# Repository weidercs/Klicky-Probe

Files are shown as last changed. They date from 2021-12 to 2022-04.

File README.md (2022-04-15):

# Klicky Probe
Microswitch probe with magnetic attachment, primarily aimed at CoreXY 3d printers.

Initially it was focused on the [Voron printers](https://vorondesign.com/) (V2.4, V1.8, Trident, V0) and derivatives, now it's been restructured to better allow other printers to be documented here.

**ATTENTION**
If you come from Voronusers please read the updated Klipper configuration on this repository

The objectives for this project are:
- drop in replacement for Omron TL-Q5MC2 or PL-08N2 (you don't need to replace the toolhead), replacement of BLtouch probes
- soldering not required
- minimal adjustments required
- be able to detect all the print surfaces
- be as close to the hotend tip as possible
- highly repeatable and accurate probes
- less temperature variations
- no melting of its parts
- cheap to build
- reuse spare parts if possible

Most of the Klicky probe users are using klipper, there are some macros in here that ease the probing process, by automating the attach, dock and use of the probe.

Some work has been developed to have the same functionality on RRF.

It can also be used with the [automatic Z calibration](https://github.com/protoloft/klipper_z_calibration) klipper plugin to effectively calculate the Z offset from the probe and from the Z endstop if your printers supports a Z endstop triggered by the nozzle (like most Voron's do)

The inspiration for the Klicky Probe comes from the [Quickdraw](https://github.com/Annex-Engineering/Quickdraw_Probe) and the [Euclid probe](https://github.com/nionio6915/Euclid_Probe), it uses some concepts from each of the projects.

Updated instructions provided by StefanRaatz.
oc_geek and TurBoxxs were also a great help in refining and testing the CAD files.
Garrettwp provided the initial revised macro files.
User richardjm revised the macro variables and added some functions.
Mental created the initial macro and one of the first magnetically attached microswitch probes.

Without them, and some others this effort would not be in the current state, many thanks to them all.

It is working very well, if you decide to use it, give me feedback, either here, or on discord, my discord user is JosAr#0517.

If you want to donate something regarding this project, use this [link](https://paypal.me/Josar154) or [__Buy me some ABS!__](https://www.buymeacoffee.com/JosAr), thanks

# Upgrading from an earlier version

If you are upgrading from an earlier version, check the [klipper macros](./Klipper_macros) folder, it contains update instructions.

# Printers With detailed instructions and specific parts (by support order)

The specific parts with install, configuration, troubleshoot and recommended settings can be found on each printer page, linked below.

[Voron v2.4](./Printers/Voron/v1.8_v2.4_Legacy_Trident)

[Voron v1.8](./Printers/Voron/v1.8_v2.4_Legacy_Trident)

[Voron Legacy](./Printers/Voron/v1.8_v2.4_Legacy_Trident)

[Voron Trident](./Printers/Voron/v1.8_v2.4_Legacy_Trident)

[Voron v0](./Printers/Voron/v0)

[VCore-3](./Printers/Ratrig/VCore3)

[MercuryOne](./Printers/ZeroG/Mercury_One)

There are also [docks and mounts submitted by users](./Usermods) to support other printers and toolheads, you should check it out.

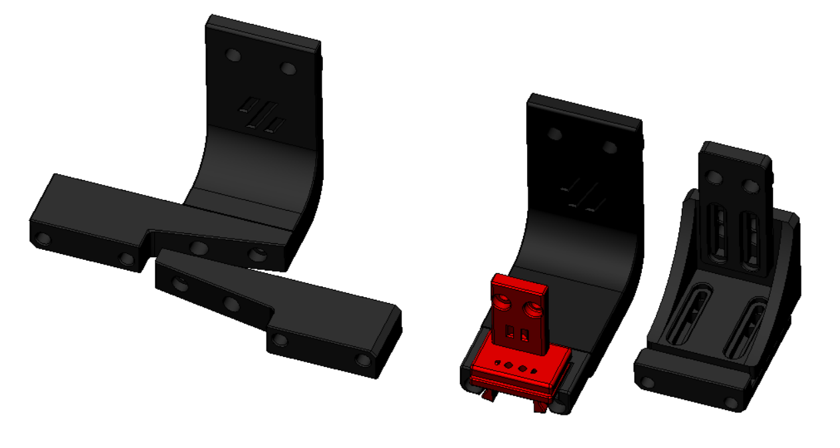
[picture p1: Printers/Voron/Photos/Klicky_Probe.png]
Klicky Probe image
klicky early version.

# Klicky components

All the compatible printers require:

* Toolhead mount (the thing that the probe attached to when it's being used)
* Klicky probe (there are three versions, all are interchangeable and compatible, more information on the specific printer page), what actually is used to probe the bed
* Probe dock (all the printers use the same)
* Probe dock mount (what attaches to the printer to dock the probe when not in use)

The CAD with all the files is located [Here](./CAD)

Common Klicky STL's (parts that are common to all the printers)  are located [here](./Base_STL).
Printer specific STL are in each printer directory.

The klipper macros are [here](./Klipper_macros), the RRF [here](./RRF_macros).

## Probe accuracy

The probe accuracy output is better than a range of 0.025mm (difference between highest and lowest), and a standard deviation of 0.01mm.

## Print Settings

There are no need for supports, recommended settings are 4 perimeters/top/bottom, at least 23% infill, the STL's are already oriented, you only need to send them to the slicer.

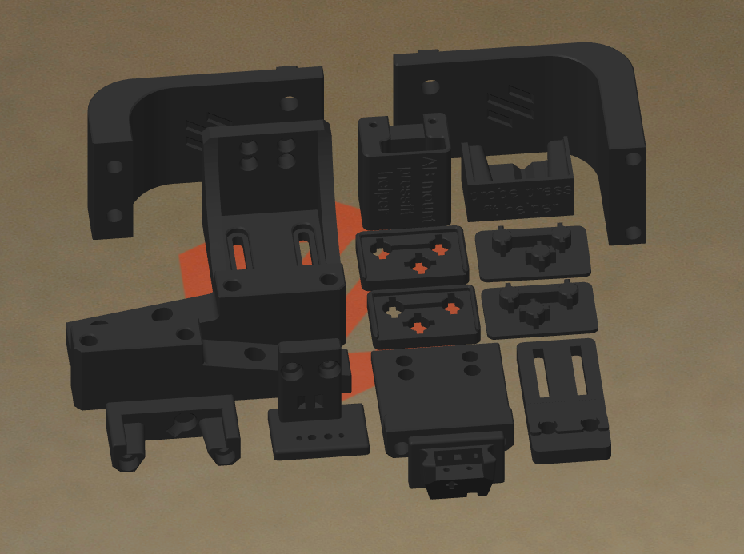
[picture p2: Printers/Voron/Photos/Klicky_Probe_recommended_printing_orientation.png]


Each printer family/version has it's own mounting options, Bill of Materials, assembly instructions and dock/attach setup.

# General Bill of Materials (BOM)

Tools:

- 1.5mm Drill (optional)
- Multimeter to check for Continuity 
- Super Glue
- Soldering Iron for the heat inserts

Probe BOM:

- 1x microswitch (the omron D2F-5 or D2F-5L (removing the lever) is recommended), D2F-1 and similar sizes microswitch also work
- 2x M2x10 mm self tapping
- some 6 mm x 3 mm magnets (it ranges from 8 to 10)
- some m5 screws
- some m3 screws
- some m3 heat inserts
- some m3 nuts

# Sourcing guide

To get the best experience, please consider purchasing from the trusted list of suppliers bellow.

[trusted suppliers list](./Sourcing.md)

# Assembled Klicky Probe on a Voron v2.4

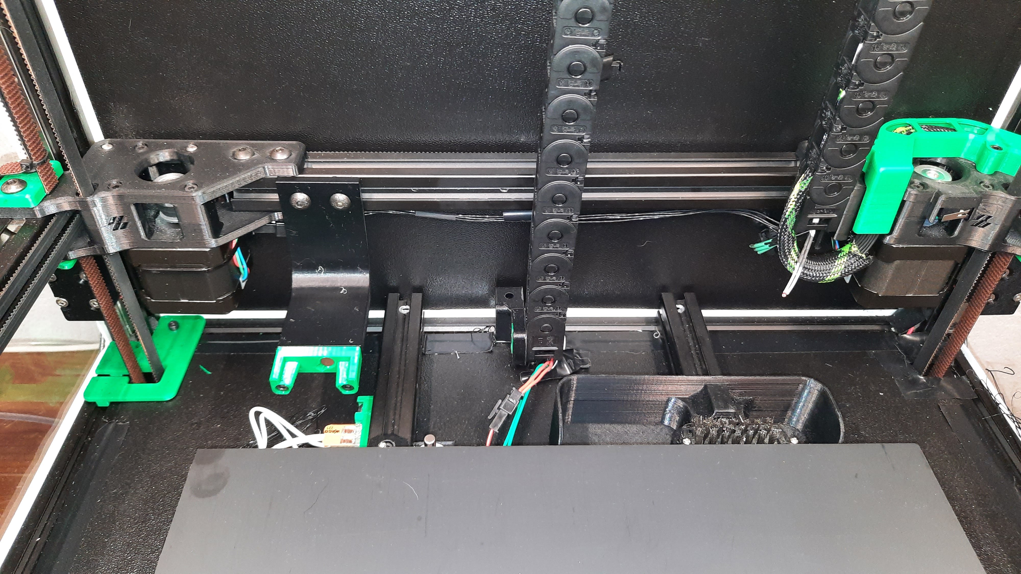
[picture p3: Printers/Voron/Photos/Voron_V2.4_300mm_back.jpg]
Assembled Klicky Probe
# 

# Dock and undock video

https://user-images.githubusercontent.com/16675722/122302371-eb9c4e00-cef9-11eb-91d3-3aded131bae0.mp4

It is working very well, if you decide to use it, give me feedback, either here, or on Voron discord, my discord user is JosAr#0517.

By standing on the shoulders of giants, lets see if we can see further.

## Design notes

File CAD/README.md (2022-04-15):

CAD files

KlickyProbe_v2_v44
Initial release of the V2 klicky, with a 2mm shorter probe dock. Probe dock mounts adjusted accordingly

KlickyProbe_v2_v50
corrected dock mount fixed distance, it was 2 mm short

KlickyProbe_v2_v51
added MercuryOne probe dock

KlickyProbe_v2_v53
added VCore3 probe dock and EVA mount

KlickyProbe_v2_v54
added V0.1 Mosquito Cowling

KlickyProbe_v2_v55
corrected V0.1 integrated Mosquito Cowlings

KlickyProbe_v2_v56
updated the probe dock to have back inserted magnets, it's not possible now for the dock magnet to touch the probe one

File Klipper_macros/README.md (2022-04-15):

# Klipper macros

These macros are  based on the great Annex magprobe dockable probe macros "#Originally developed by Mental, modified for better use on K-series printers by RyanG and Trails", kudos to them.
That macro as since evolved into a klipper plugin that currently is pending inclusion in klipper, more information [here](https://github.com/Annex-Engineering/Quickdraw_Probe/tree/main/Klipper_Macros)

Would alse like to thank the Voron discord community and VoronDesign for all the work, suggestions and support that they have given to improve on the macros.

## Updating from an earlier version

While you should read these instructions to the end, as the necessary helper functions are now split on different files and it's better explained below, as a current user of the klicky macros, it's easier to configure.

The first macro on the old klicky-probe.cfg contained all the necessary variables, you should the values you changed one by one to the new klicky-variables.cfg, the most important are these ones:

```python
# if you do not have any of these variables, read the explanation on klicky-variables.cfg and the setup of the macros on your respective printer, this is a quick start quide
variable_enable_z_hop           # set this to false for beds that fall significantly under gravity (almost to Z max)
variable_max_bed_y              # bed max y size
variable_max_bed_x              # bed max x size

variable_z_endstop_x            # copy this value over your old file
variable_z_endstop_y            # copy this value over your old file

variable_docklocation_[x,y,z]   # copy this value over your old file
Variable_dockmove_[x,y,z]       # use 40,0,0 it's the old default
Variable_attachmove_[x,y,z]     # use 0,30,0 it's the old default
```

Now if you use auto-z calibration, you also should copy z-calibration.cfg to klicky-z-calibration.cfg and remove the z-calibration.cfg include in printer.cfg.

## New installation

The macros are currently separated by function, there is klicky-probe.cfg that should include the remaining files, this both keeps klipper's printer.cfg cleaner and allow for backward compatibility.

The remaining files are the klicky-macros.cfg that stores all the general macros (like the dock and attach macros, this file is required on all the printers), the klicky-variables.cfg where it's necessary to configure the dock location and do other printer specific configurations and the klipper helper files for specific functions.

The helper files work by expanding the standard klipper function with a attach and dock command, so that you can use all the klipper commands without the need to manually attach and dock the printer.

Right now the macros are divided in multiple files, that way it is much easier to upgrade, configure and maintain

| File | v2.4 | v1.8 | Legacy | Trident | v0 | Tiny-M | V-core3 | MercuryOne |
| --- | :---: | :---: | :---: | :---: | :---: | :---: | :---: | --- |
| klicky-probe.cfg | :heavy_check_mark: | :heavy_check_mark: | :heavy_check_mark: | :heavy_check_mark: | :heavy_check_mark: | :heavy_check_mark: | :heavy_check_mark: | :heavy_check_mark: |
| klick-variables.cfg | :heavy_check_mark: | :heavy_check_mark: | :heavy_check_mark: | :heavy_check_mark: | :heavy_check_mark: | :heavy_check_mark: | :heavy_check_mark: | :heavy_check_mark: |
| klicky-bed-mesh-calibrate.cfg | :heavy_check_mark: | :heavy_check_mark: | :heavy_check_mark: | :heavy_check_mark: | :heavy_check_mark: | :heavy_check_mark: | :heavy_check_mark: | :heavy_check_mark: |
| Klicky-quad-gantry-level.cfg | :heavy_check_mark: | :x: | :x: | :x: | :x: | :x: | :x: | :x: |
| Klicky-screws-tilt-calculate.cfg | :x: | :heavy_check_mark: | :heavy_check_mark: | :x: | :heavy_check_mark: | :heavy_check_mark: | :x: | :grey_question: |
| klicky-z-tilt-adjust.cfg | :x: | :heavy_check_mark: | :heavy_check_mark: | :heavy_check_mark: | :x: | :x: | :heavy_check_mark: | :heavy_check_mark: |

* klicky-probe.cfg (includes all the necessary files in klipper)
* klick-variables.cfg, stores all the Klicky variables, printer specific, should not be necessary to update very often
* klicky-bed-mesh-calibrate.cfg, bed mesh helper scripts, assumes bed mesh is already configured, includes a commented example, further help on setup [here](https://www.klipper3d.org/Bed_Mesh.html#bed-mesh)
* Klicky-quad-gantry-level.cfg, Quad Gantry Level helper script, allows on machines with four Z independent motors to level the bed automatically, assumes QGL is already configured (it's used on a V2.4 to level the gantry relative to the bed), further help [here](https://www.klipper3d.org/Config_Reference.html?h=quad#quad_gantry_level)
* Klicky-screws-tilt-calculate.cfg, screws tilt adjust helper script, knowing where the bed screws are, it will assist in leveling the bed by calculating on the number of times each screw should be rotated, assumes that the configuration is already defined, further help on setup [here](https://www.klipper3d.org/Manual_Level.html#adjusting-bed-leveling-screws-using-the-bed-probe)
* klicky-z-tilt-adjust.cfg, Z tilt adjust helper script, allows on machines with two or three Z independent motors to level the bed automatically, assumes that the configuration is already defined, further help on setup [here](https://www.klipper3d.org/Config_Reference.html?h=z_tilt#z_tilt)
* klicky-specific.cfg, place to put other configurations specific to your printer, like probe or bed mesh klipper configuration

Some printers, like the Voron v0 or Tiny-M don't have the probe as a standard configuration, so in those printers documentation there are extra klipper configurations that you need to use in order to configure the actual probe.

## printer.cfg configuration 

Download the appropriate files (or the zip containing them all and delete the ones that are not relevant) and upload it to your klipper Config folder.

```
cd ~/klipper_config/
wget https://raw.githubusercontent.com/jlas1/Klicky-Probe/main/Klipper_macros/Klipper_macros.zip
unzip Klipper_macros.zip
```

Check the klicky-probe.cfg, remove or comment the macros that are not required for your printer or that you do not want to implement.
Edit klicky-variables.cfg (there are printers specific recommendations on the printer configuration page) for klicky to operate properly.

There are some configurations that need to be checked, otherwise your will run into **out of range** problems, that is by design.

Open your printer.cfg file, comment out *safe_z_home* or *homing_override*, if you have them (the macros will take care of homing) and add the following line before the "Macros" Section.

`[include klicky-probe.cfg]`

It should look like this:

```
#####################################################################
# 	Macros
#####################################################################
[include klicky-probe.cfg]
```

You now need to configure the probe pin, that is printer specific, and the details are on your printer configuration guide.

Regarding you print start and end macros, with the helper scripts implemented, they do not need to be changed.

If however you would like to reduce the times that the toolhead attaches and docks the probe, you can use Attach_Probe_Lock that prevents the probe to be docked after an operation that normally would dock the probe.

**BEWARE that the probe may hit the bed depending on what you are doing**.

When you don't need the probe attached anymore, run Dock_Probe_Unlock to dock and unlock the probe.

## Pre and Post macros for dock operations

If your setup requires a custom move, a macro to be called before attaching and docking, there are two macros \_DeployDock and \_RetractDock that are executed (if they are configured) when it's required for the dock to be ready for docking and attachment operations.

## XY Sensorless homing 

If you are using sensorless homing, and have your own X and/or Y homing macros, you can use override the klicky macros behavior with your very own _HOME_X and _HOME_Y macros.

If they exist on your klipper configuration, klicky macro will use them instead of the default G28 commands.

## Advanced users

**Beware going forward, you will leave the safety that the macros provide**

I recognize that some users are very technical and may want to write custom macros, so here are the only commands that you need to  attach and dock the probe, without any fail safes or checks.

### Probe attach commands

```python
# Probe entry location
G0 X{docklocation_x|int - attachmove_x|int - attachmove2_x|int} Y{docklocation_y|int - attachmove_y|int - attachmove2_y} F{travel_feedrate}
# Attach probe
G0 X{docklocation_x|int - attachmove2_x|int} Y{docklocation_y|int - attachmove2_y} F{travel_feedrate}
G0 X{docklocation_x} Y{docklocation_y} F{dock_feedrate}
# Probe exit location
G0 X{docklocation_x|int - attachmove_x|int} Y{docklocation_y|int - attachmove_y|int} F{release_feedrate}
```

### Probe dock commands

```python
# Probe entry location
G0 X{docklocation_x|int - attachmove_x|int} Y{docklocation_y|int - attachmove_y|int} F{travel_feedrate}
# Drop Probe to Probe location
G0 X{docklocation_x} Y{docklocation_y} F{dock_feedrate}
# Probe decoupling
G0 X{docklocation_x|int + dockmove_x|int} Y{docklocation_y|int + dockmove_y|int} F{release_feedrate}
G0 X{docklocation_x|int + dockmove_x|int - attachmove_x|int} Y{docklocation_y|int + dockmove_y|int - attachmove_y|int} F{release_feedrate}
```

The typical variables values are:

variable_travel_speed:          100    # how fast all other travel moves will be performed when running these macros
variable_dock_speed:             50    # how fast should the toolhead move when docking the probe for the final movement
variable_release_speed:         75    # how fast should the toolhead move to release the hold of the magnets after docking
variable_docklocation_x:                 # X Dock position
variable_docklocation_y:                 # Y Dock position
#Dock move (if the dock is mounted on the back extrusion, these values can be left untouched)
Variable_dockmove_x:              0    # Final toolhead movement to release
Variable_dockmove_y:            40    # the probe on the dock
Variable_dockmove_z:              0    # (can be negative)
#Attach move (if the dock is mounted on the back extrusion, these values can be left untouched)
Variable_attachmove_x:          30    # Final toolhead movement to Dock
Variable_attachmove_y:            0    # the probe on the dock
Variable_attachmove_z:            0    # (can be negative)

Variable_attachmove2_x:          0    # intermediate toolhead movement to attach
Variable_attachmove2_y:          0    # the probe on the dock (can be negative)
Variable_attachmove2_z:          0    # (to be used as a last move before attaching the probe, suitable for Euclid)

**Again, be advised that these will not raize the bed to avoid hitting it, won't check if the probe is docked or attached. USE EXTREME CAUTION**

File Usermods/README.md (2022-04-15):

# Klicky usermods

Here you can find Klicky user submitted mods to support extra printers and toolheads, mods that support a printer with specific documentation (Like the Vorons ot the Vcore3) have a dedicated usermod directory in the specific printer directory.

All the compatible printers require:

* Toolhead mount (the thing that the probe attached to when it's being used), it's toolhead specific
* Klicky probe (there are three versions, all are interchangeable and compatible, more information on the specific printer page), what actually is used to probe the bed, the parts are equal on all the printers
* Probe dock (all the printers use the same), the parts are equal on all the printers
* Probe dock mount (what attaches to the printer to dock the probe when not in use), should be printer specific and not toolhead specific

The recommended macros can be found [here for klipper](..//Klipper_macros) macros and [here for RRF](../RRF_macros).

There are two types of user mod:

* Printer dock mount (identified by "dock mount")
* Toolhead probe mount (identified by "probe mount")

| Owner | Descrption | Mod Type | Printer/Toolhead |
| --- | --- | --- | --- |
| TheMacBoy | [support arm for Ender 5 Plus with rails](./TheMacBoy) | dock mount  | Ender 5 Plus |
| TheMacBoy | [Klicky Probe mount for EVA](./TheMacBoy) | probe mount | EVA 2.2+ |
| DoubleT | [Klicky Probe mount for EVA Trihorn UHF fan duct](./DoubleT) | probe mount | EVA 2.4+ |

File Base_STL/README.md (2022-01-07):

# STL files for common parts for Klicky probe

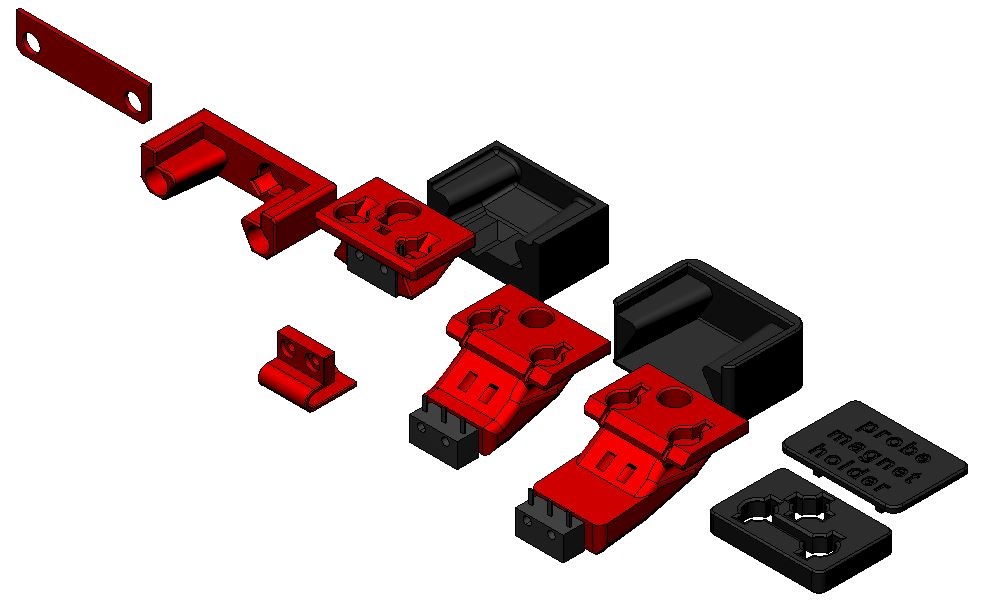
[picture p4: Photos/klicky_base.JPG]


Here you can find the parts that are common across all printers-

There is no need for supports, all the files are ready to print, they are in the recommended orientation, the standard probe (KlickyProbe_v2.stl) can also be printed with the magnet hole facing down without supports.
You can also use brim on the probes to help with bed adhesion.

- Version 0.1 - initial release
- Version 0.2 - Revised probe and dock to improve the docking fit, remaining components are compatible
  - Thanks to oc_geek for improving the probing of a badly tilted gantry (10º) and the probe and dock attachment, it's much better now
- Version 2
  - Reduced the dock by 2mm, extended the dock mounts by 2mm
  - Added two new probes, one mostly for Voron v0 the oher for Tiny-M, they extend the original by different lengths below the nozzle

The Klicky Probe consists on four different components:
- Toolhead mount, found on the printer specific STL directory
- the probe itself
- probe dock
- Frame dock mount, found on the printer specific STL directory

The recommended printing configuration are:

* initial layer height:0,24
* layer height: 0.2mm
* bottom/top/perimeters: 4
* infill: more than 23%
* infill type: Cubic
* Thin walls: On

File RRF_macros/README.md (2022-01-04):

I have zero experience with RRF, but Noodle obviously knows and has done the necessary work to get both klicky and [autoZ](https://github.com/protoloft/klipper_z_calibration) working.

You can look up the firmware configuration on a Voron v2.4 for the [Klicky RRF macros](https://github.com/pRINTERnOODLE/RRF-klicky-probe-voron-2.4.git) and for the [Klicky plus AutoZ](https://github.com/pRINTERnOODLE/Auto-Z-calibration-for-RRF-3.3-or-later-and-Klicky-Probe).

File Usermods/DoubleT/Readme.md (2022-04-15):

## Description
This is a modification of Klicky probe to be used in the 2.4 EVA carriage fan duct.

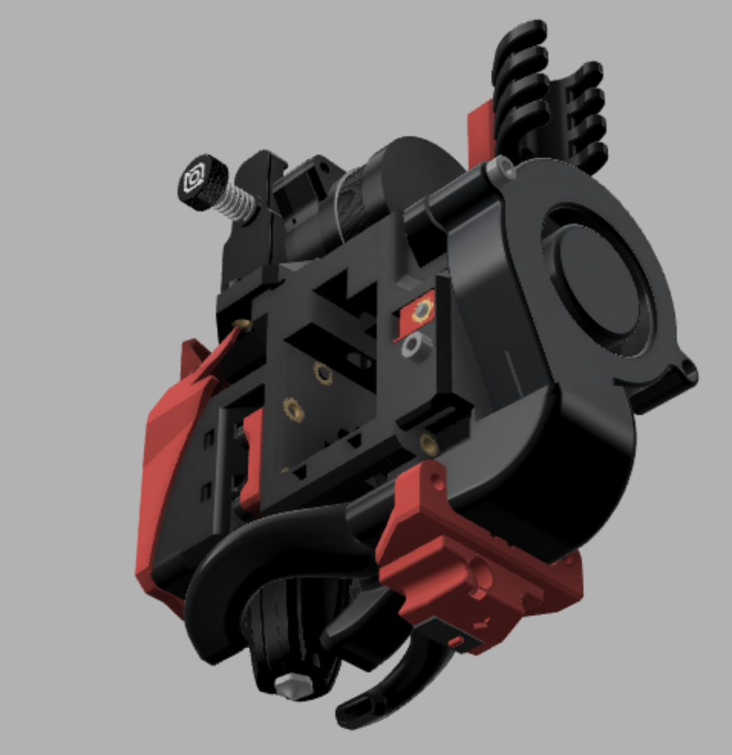
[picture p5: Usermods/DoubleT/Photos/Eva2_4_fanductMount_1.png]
Klicky probe bottom


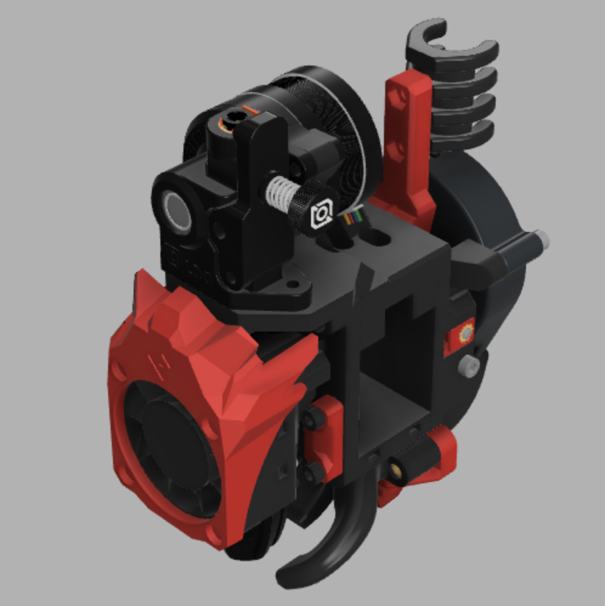
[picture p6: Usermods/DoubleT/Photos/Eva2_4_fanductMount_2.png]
Klicky probe top


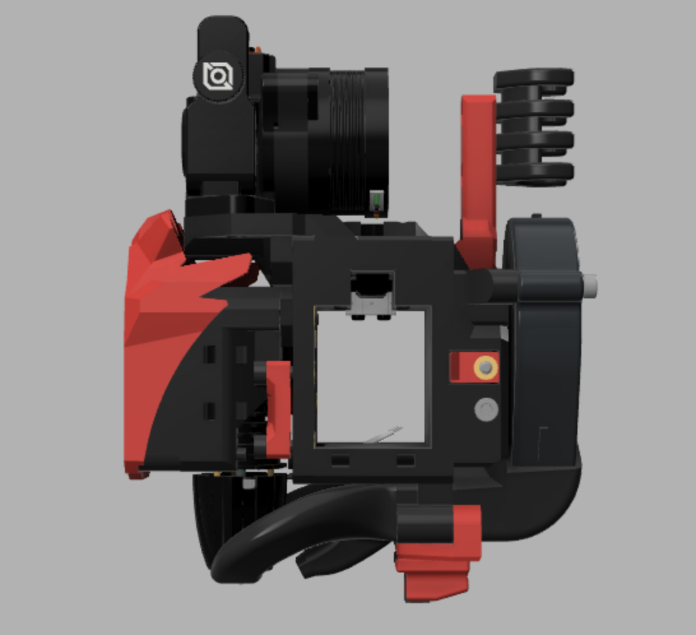
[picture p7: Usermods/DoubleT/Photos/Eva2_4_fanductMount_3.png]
Klicky probe side


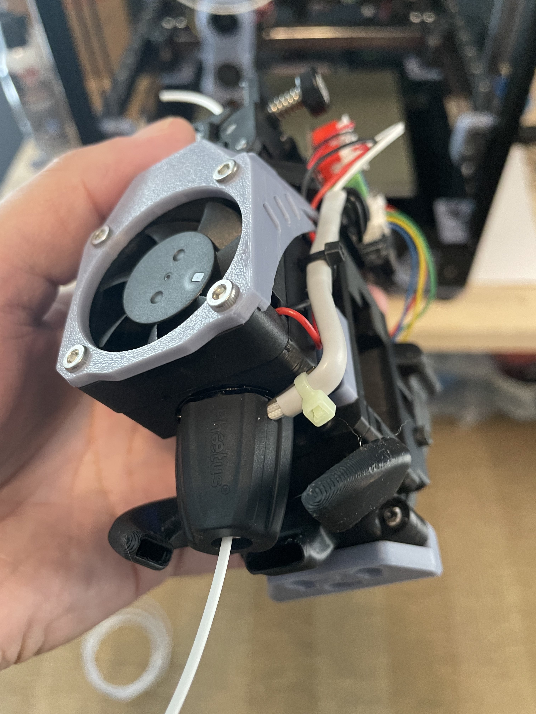
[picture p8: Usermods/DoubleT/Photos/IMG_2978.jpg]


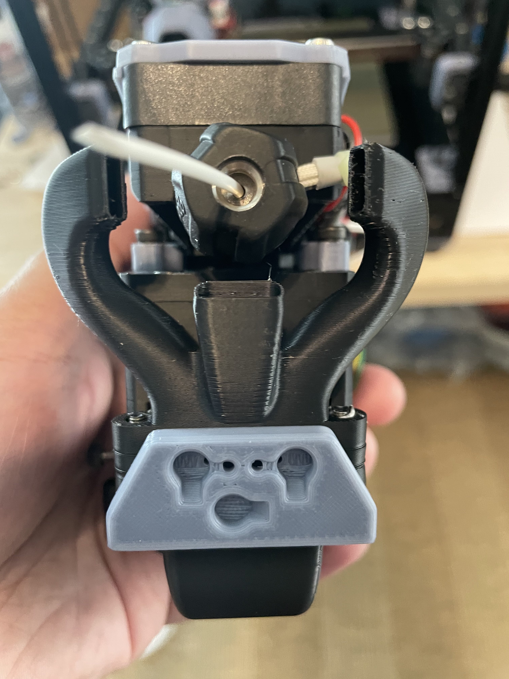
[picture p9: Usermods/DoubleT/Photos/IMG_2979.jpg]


## Compatible EVA version
2.4.0 - ?

## Related EVA parts
back_corexy, Trihorn UHF fan duct

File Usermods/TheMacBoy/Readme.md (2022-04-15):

---
title: TheMacBoy's Klicky Probe mount for EVA and Ender 5 Plus (with rails) compatibility
---

> Created by: [TheMacBoy](https://github.com/themacboy)

## Description
This is a modification of Klicky probe to be used in the EVA carriage, plus support arm for Ender 5 Plus with rails.

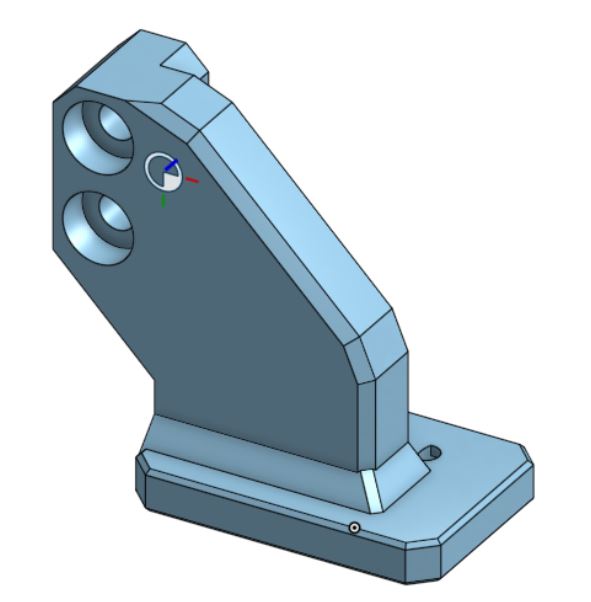
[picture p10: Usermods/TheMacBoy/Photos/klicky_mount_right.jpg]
Klicky probe right


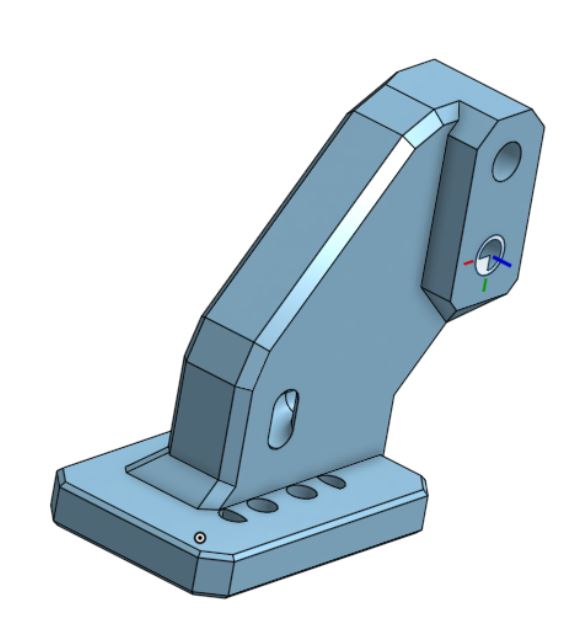
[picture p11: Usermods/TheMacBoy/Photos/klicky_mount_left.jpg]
Klicky probe left


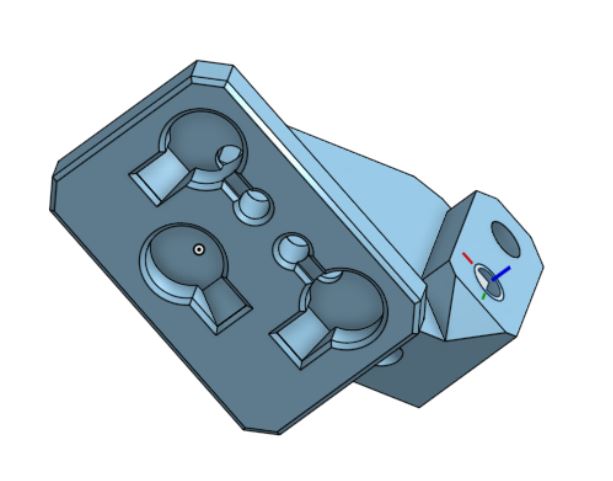
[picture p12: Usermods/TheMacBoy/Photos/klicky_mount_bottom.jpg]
Klicky probe bottom


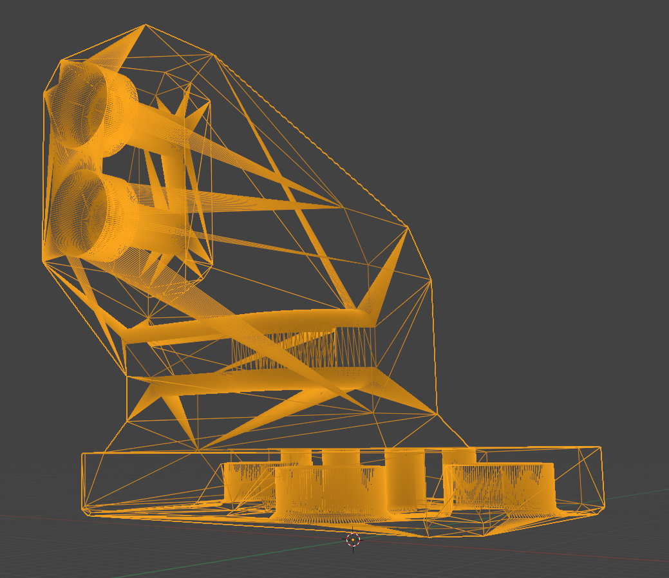
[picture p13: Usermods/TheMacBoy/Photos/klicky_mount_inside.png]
Klicky probe inside


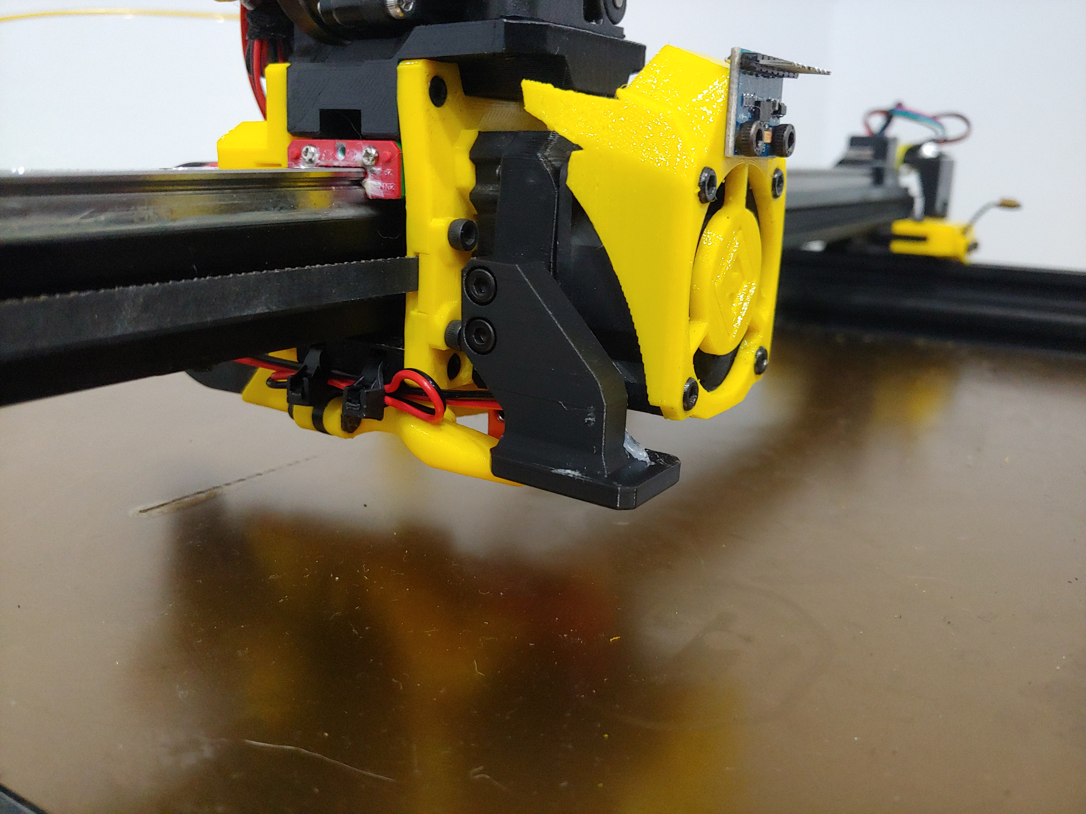
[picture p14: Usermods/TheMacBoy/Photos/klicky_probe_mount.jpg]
Klicky probe


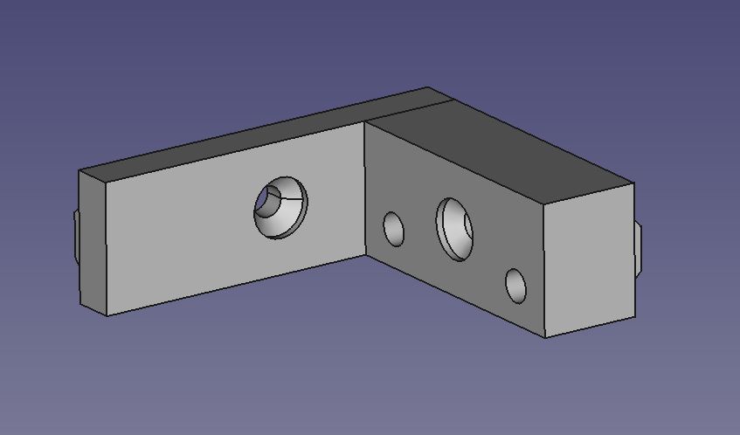
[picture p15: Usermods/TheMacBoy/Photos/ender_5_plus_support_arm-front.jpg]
Ender 5 Plus support arm front


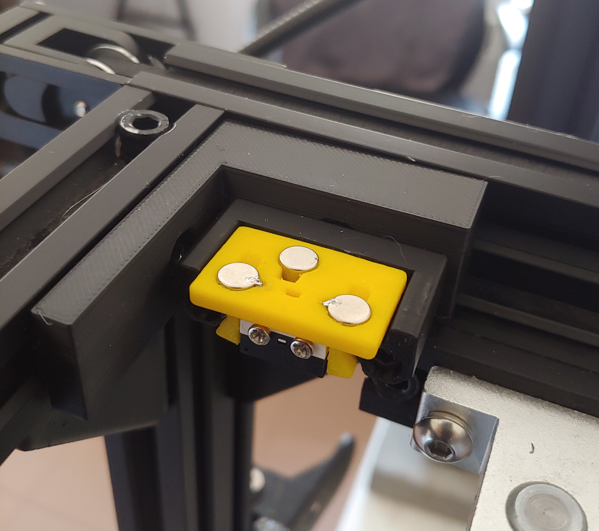
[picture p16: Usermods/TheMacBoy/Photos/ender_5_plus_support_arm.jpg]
Ender 5 Plus support arm


## Compatible EVA version
2.2.0 - ?

## Related EVA parts
universal_face

## Source Klicky probe files
[Klicky Probe](../../Base_STL)

## Source OnShape files
[Klicky mount for Eva ](https://cad.onshape.com/documents/2fc54d83c144f64dfbd5b70d/w/5a27aacdedad8aa85274c7e9/e/03e92f0ea05a500c94d12e60)

## Source FreeCad files
Ender-5 Plus arm support inside cad folder

## Changelog
v0.5 30/12/2021 TheMacBoy Release

v0.6 09/01/2022 Klicky probe modified the back size of the frame support, new version v.2

16/02/2022 Added my custom "klicky-variables.cfg" macro as example (my custom settings on my custom Ender-5 Plus ;)

## BOM Parts:
| No | Qty | Name | Printable |
| -- | --- | --- | --- |
| 1  | 1 | Eva-2.2 Klicky probe mount | [Yes](EVA_2.2^/stl/eva-2.2-klicky_probe_mount.stl) |
| 1  | 1 | Ender-5 Plus support arm v.1 | [Yes](Ender-5_(pro,plus)/stl/ender_5_plus-arm_v.1-body.stl) |
| 1  | 1 | Ender-5 Plus support arm v.2 | [Yes](Ender-5_(pro,plus)/stl/ender_5_plus-arm_v.2-body.stl) |

## STEP format:
| No | Qty | Name | Printable |
| -- | --- | --- | --- |
| 1  | 1 | Eva-2.2 Klicky probe mount | [Yes](EVA_2.2^/cad/eva-2.2-klicky_probe_mount.step) |
| 1  | 1 | Ender-5 Plus support arm v.1 | [Yes](Ender-5_(pro,plus)/cad/ender_5_plus-arm_v.1-body.step) |
| 1  | 1 | Ender-5 Plus support arm v.2 | [Yes](Ender-5_(pro,plus)/cad/ender_5_plus-arm_v.2-body.step) |

## BOM screws:
| Qty | Name | Observations |
| --- | --- | --- |
| 2 | M3 20mm | (hex head) |
| 1 | M4 20mm | (countersunk head) |
| 1 | M4 10mm | (countersunk head) |
| 2 | M4 T-Nut | |
| 2 | M3 12mm | (hex head) |
| 2 | M3 nuts | |
| 2 | M2 10mm | carpentry type |
| 2 | M3 inserts x D5 x L5 | |

## Hardware Required 
Standard EVA

Ender-5 Plus

## To Do 
pending to draw arm on OnShape

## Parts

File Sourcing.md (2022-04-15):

# Trusted suppliers

The following shops are all responsive and helpful, they can help with the sourcing of the required parts for your klicky probe.

| **Shop** |  **Location** | Hadware Kits | Parts | Klicky printed parts | Comments |
| --- | :---: | :---: | :---: | :---: | --- |
| [Fabrekko](https://www.fabreeko.com) | :us: | :heavy_check_mark: | some | :x: | lots of parts to expand 3d printers |
| [Lab4450](https://lab4450.com/) | :eu: :portugal: | :heavy_check_mark: | :x: |  :heavy_check_mark:  | kits for V0, V2, VT, Vcore, PCB's |
| [Vonwange](https://vonwange.com/) | :eu: :de: | :heavy_check_mark: | :heavy_check_mark: |  :heavy_check_mark:  | lots of parts to expand 3d printers |
| [Replimat](https://www.replimat.eu)  | :eu: :de: | :heavy_check_mark: | :heavy_check_mark: | :x: | specializes in some hard to find items |
| [KB-3D](https://kb-3d.com) | :us: | :heavy_check_mark: | :heavy_check_mark: | :x: | specializes in Open source community builds and parts|

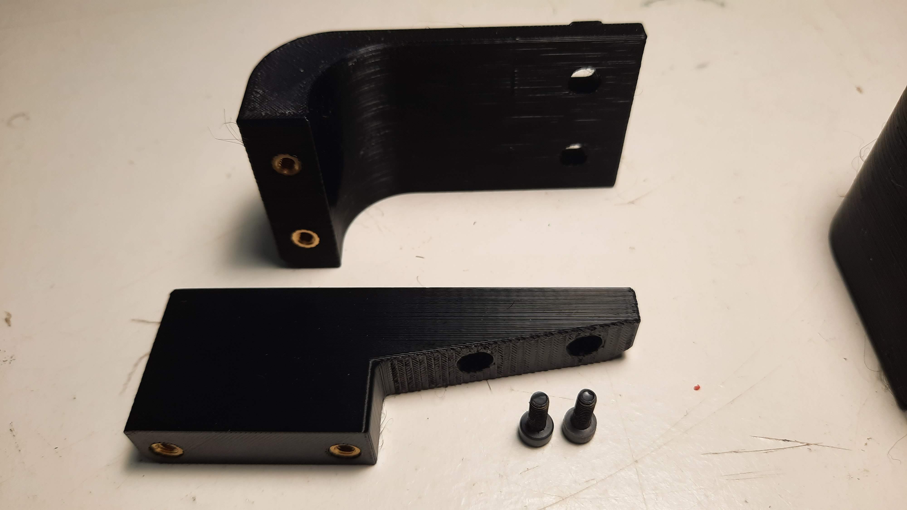
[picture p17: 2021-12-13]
Printers/Voron/Photos/gantry_fixed_dock_sidemount_components.jpg

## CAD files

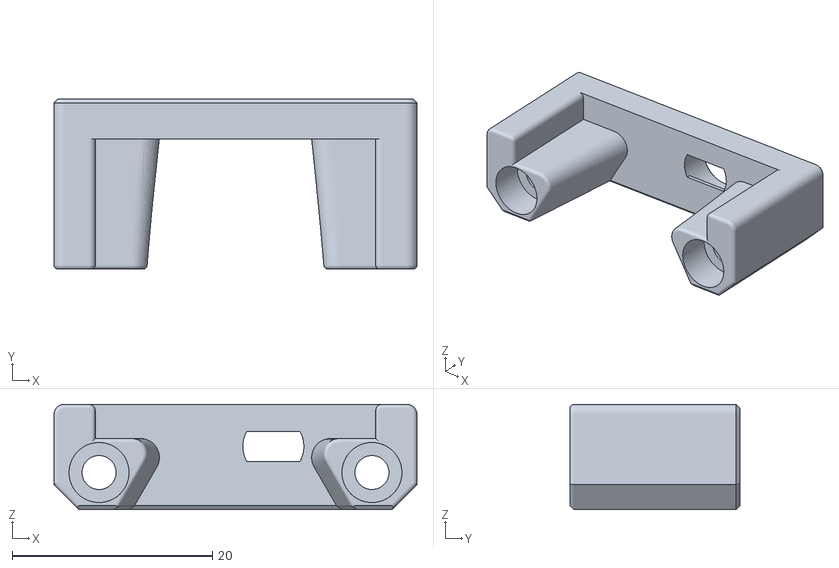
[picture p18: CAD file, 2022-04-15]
Base_STL/Probe_Dock_v2.1.stl
36.3 x 17.0 x 10.5

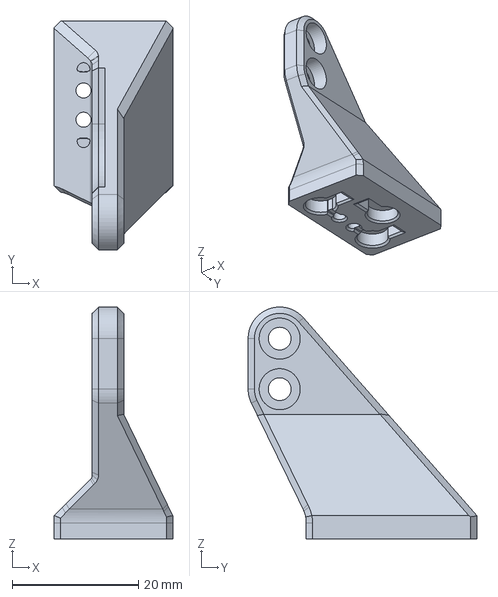
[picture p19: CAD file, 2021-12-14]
Printers/Ratrig/Vcore-3/CAD/Eva probe bracket v15.step
18.8 x 36.2 x 36.7 mm

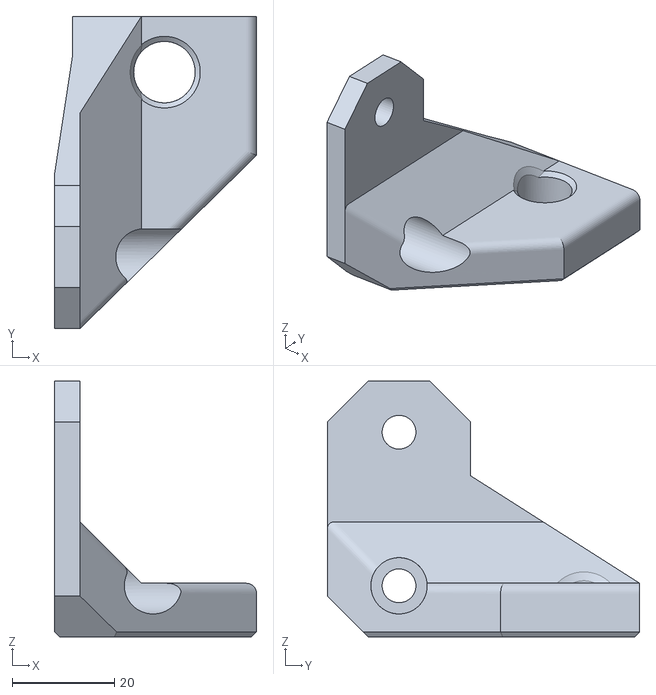
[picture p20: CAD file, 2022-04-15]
Printers/Ratrig/VCore3/VCore3_STL/probe_dock_mount.stl
39.5 x 61.0 x 50.0

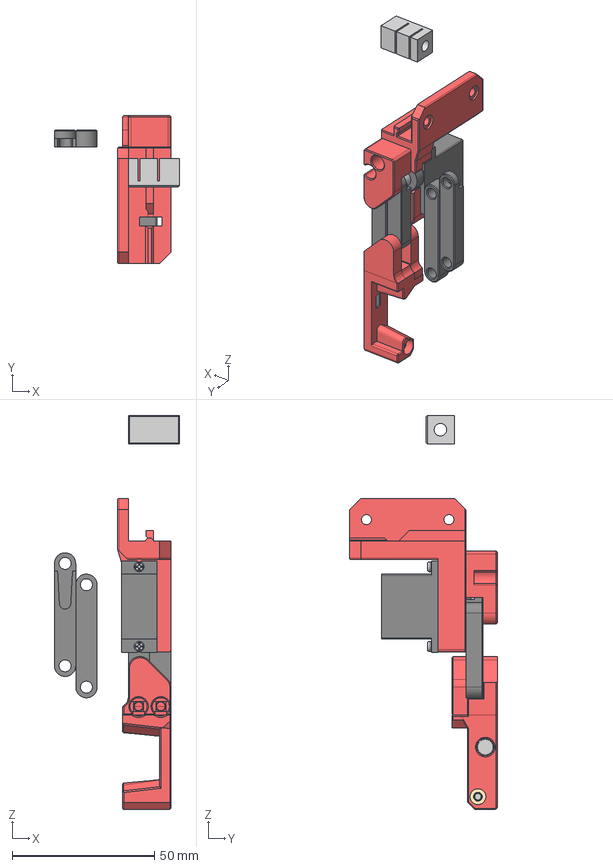
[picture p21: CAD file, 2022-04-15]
Printers/Voron/v0/Usermods/KlickSwipe/CAD/KlickSwipe.step
44.0 x 52.1 x 138.5 mm
Tube Cutting Jig
Free Arm - 22mm
Free Arm - 32mm
Drive Arm - 22mm
Drive Arm - 32mm
Servo Mount Top
6mm x 3mm Round Neodymium Magnet
M3x12 BHCS
M3 Threaded Insert x 5
Klicky Dock Bottom
Servo Mount Body
Servo Arm
M3x8 BHCS x 4
4mm x 14mm PTFE Tube x 3
4mm x 7mm PTFE Tube
M2 Self Tapping Screw x 2

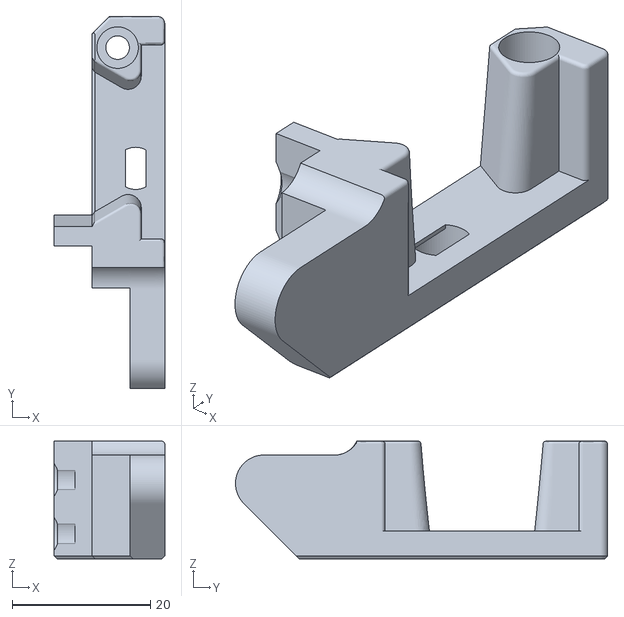
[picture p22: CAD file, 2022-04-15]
Printers/Voron/v0/Usermods/KlickSwipe/STL/[a]_klicky_dock_x1.stl
16.0 x 53.8 x 17.0

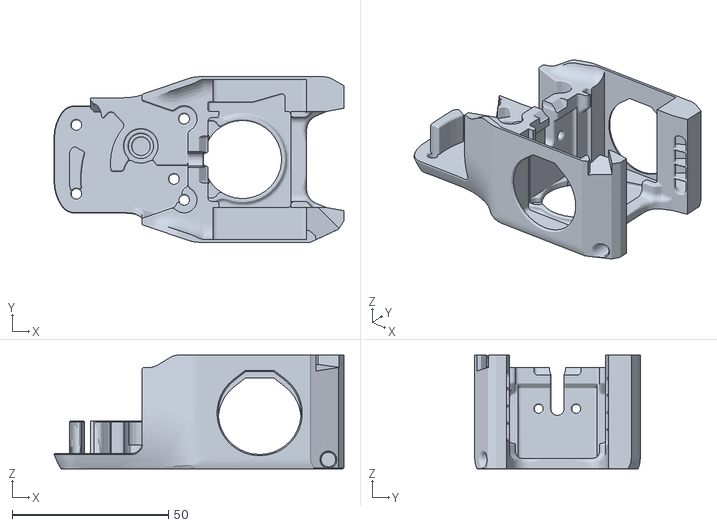
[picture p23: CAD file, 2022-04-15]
Printers/Voron/v0/v0_STL/Skeeter_Cowling_wKlicky_.stl
92.8 x 53.0 x 36.5

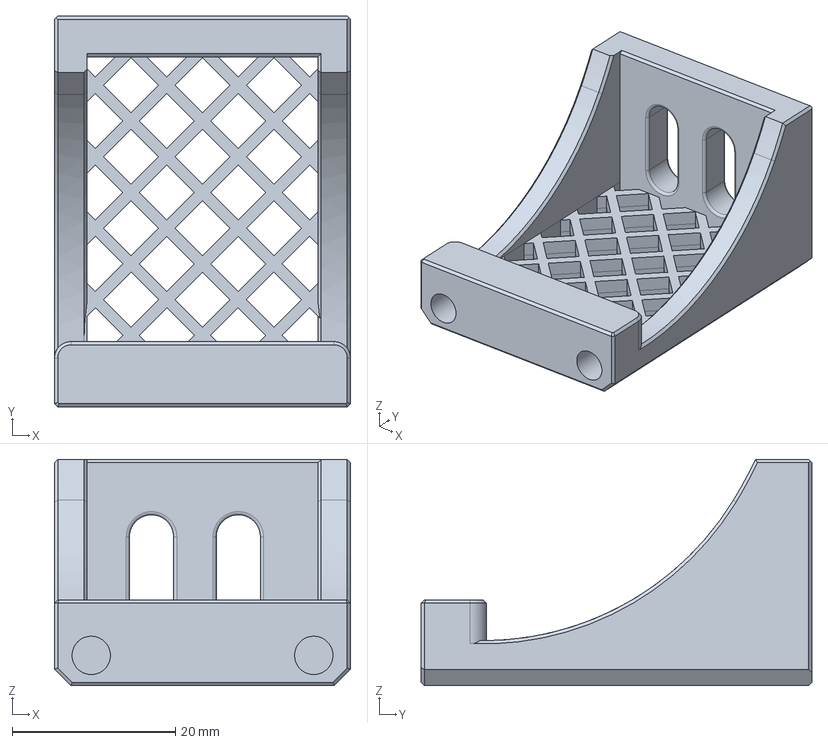
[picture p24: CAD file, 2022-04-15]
Printers/ZeroG/Mercury_One/Voron_Toolhead_CAD/Dock_mount_Ender5.step
36.3 x 47.9 x 27.7 mm

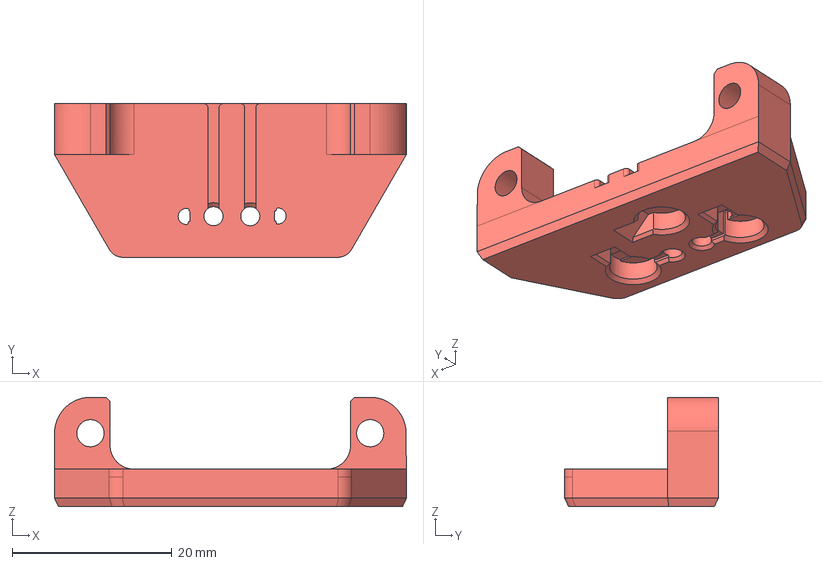
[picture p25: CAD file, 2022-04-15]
Usermods/DoubleT/CAD/Klicky_-_Eva_2.4_mount.step
44.0 x 19.2 x 13.7 mm

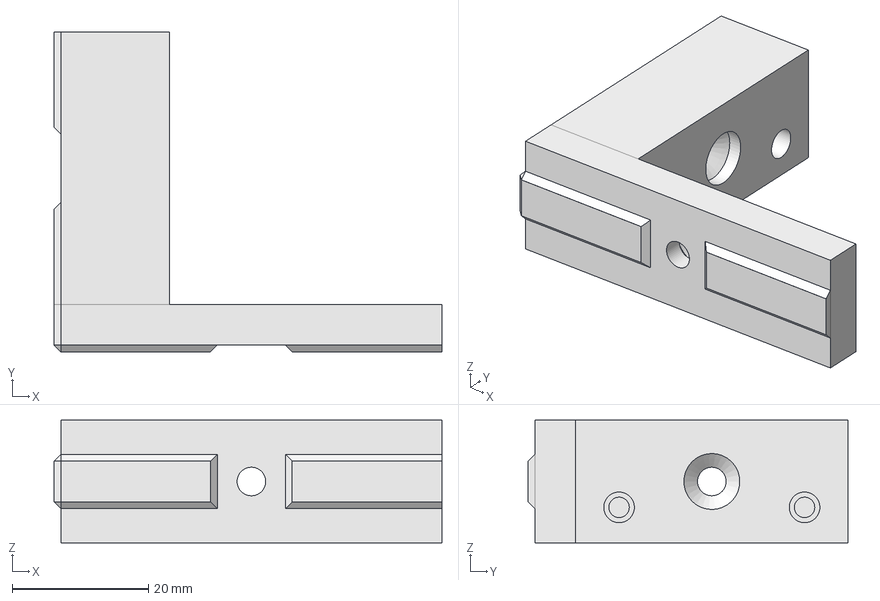
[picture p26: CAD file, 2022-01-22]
Usermods/TheMacBoy/Ender-5_(pro,plus)/cad/ender_5_plus-arm_v.2.FCStd
57.0 x 47.0 x 18.0 mm

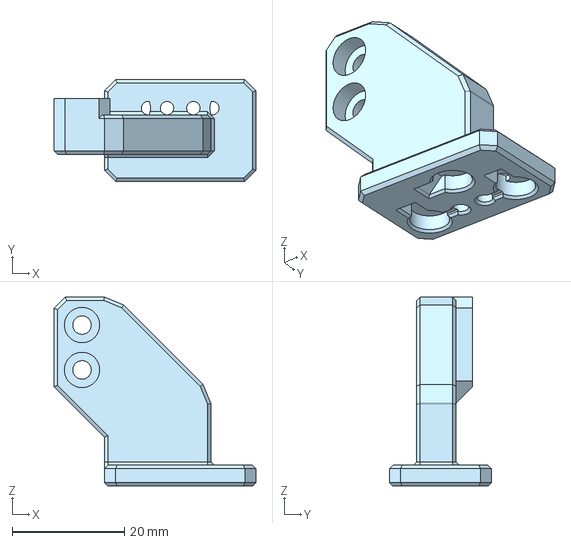
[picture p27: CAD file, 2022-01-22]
Usermods/TheMacBoy/EVA_2.2^/cad/eva-2.2-klicky_probe_mount.step
36.0 x 18.2 x 33.7 mm

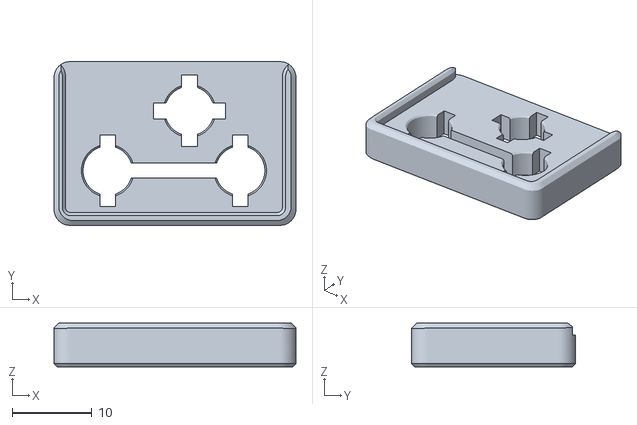
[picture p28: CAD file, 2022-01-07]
Base_STL/Probe_magnet_holder.stl
30.4 x 20.6 x 5.50

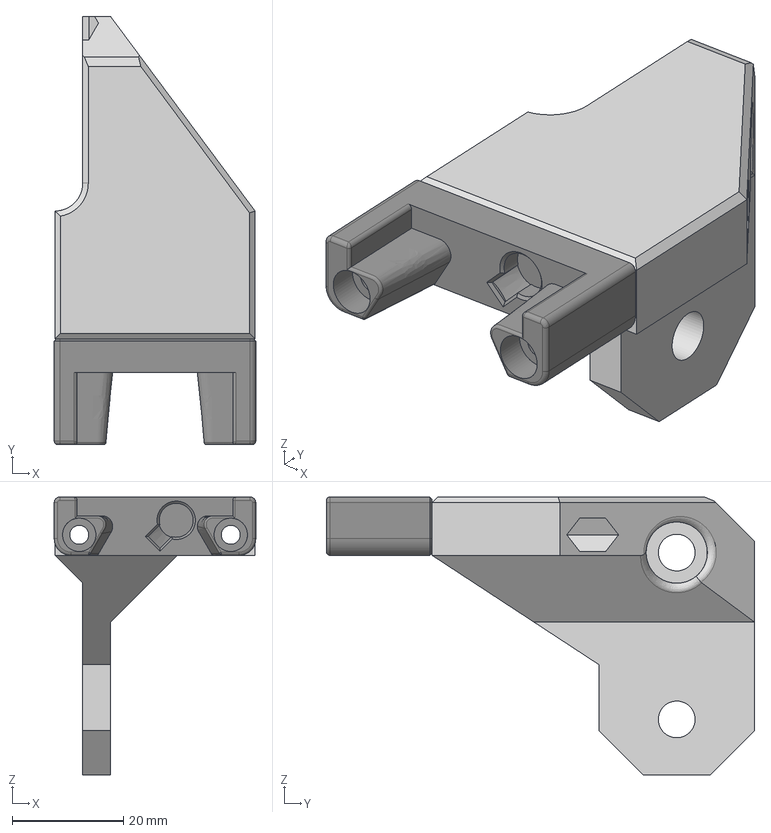
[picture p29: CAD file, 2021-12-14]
Printers/Ratrig/Vcore-3/CAD/KlickyProbe_Dock_Mount_VCore3.step
36.3 x 77.0 x 50.0 mm

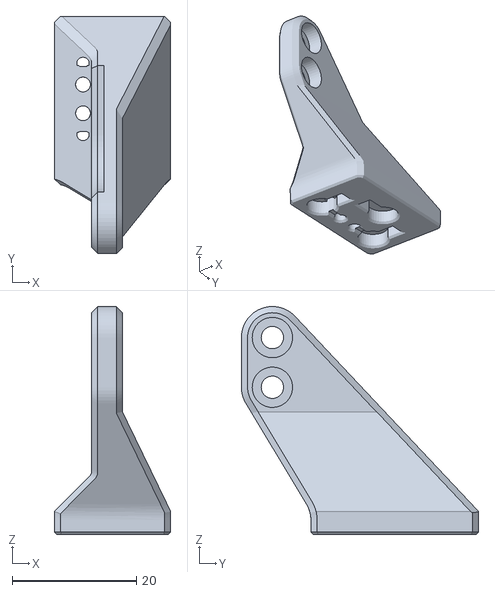
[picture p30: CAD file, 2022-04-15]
Printers/Ratrig/VCore3/VCore3_STL/probe_mount.stl
18.8 x 38.2 x 36.7

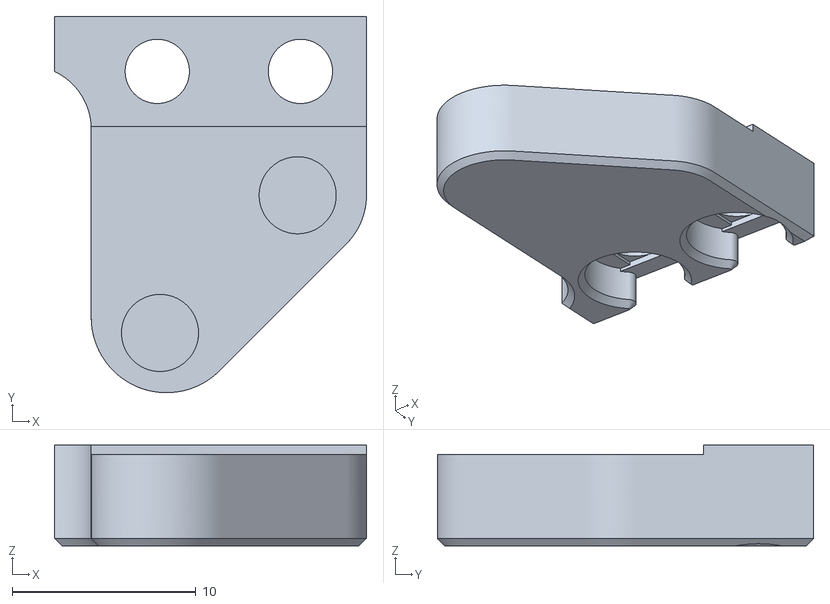
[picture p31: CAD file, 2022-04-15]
Printers/Voron/v0/Usermods/KlickSwipe/STL/[a]_klicky_dock_bottom_x1.stl
17.0 x 20.5 x 5.48

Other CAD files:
Printers/Ratrig/Vcore-3/STL/KlickyProbe_EVA_Mount.stl
Usermods/DoubleT/Stl/Klickymount_EVA_fanduct.stl
Printers/Voron/v0/v0_STL/Sherpa_Mini_Mosquito_Cowling_wKlicky.stl
Usermods/TheMacBoy/Ender-5_(pro,plus)/cad/ender_5_plus-arm_v.1-body.step
Base_STL/1mm_Spacer.stl
Base_STL/KlickyProbe_Long_v2.stl
Base_STL/KlickyProbe_Longer_v2.stl
Base_STL/KlickyProbe_v2.stl
Base_STL/Longer_probe_pressfit_helper.stl
Base_STL/Probe_magnet_pressfit_helper.stl
Base_STL/Probe_pressfit_holder.stl
Base_STL/Switch_extender.stl
Printers/Ratrig/Vcore-3/CAD/Eva probe bracket v15.f3z
Printers/Ratrig/Vcore-3/CAD/KlickyProbe_Dock_Mount_VCore3.f3z
Printers/Ratrig/Vcore-3/STL/KlickyProbe_Dock_Mount_VCore3.stl
Printers/Voron/v0/Usermods/KlickSwipe/CAD/KlickSwipe.f3d
Printers/Voron/v0/Usermods/KlickSwipe/STL/[a]_ptfe_tube_cutting_jig_x1.stl
Printers/Voron/v0/Usermods/KlickSwipe/STL/[a]_servo_mount_top_x1.stl
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

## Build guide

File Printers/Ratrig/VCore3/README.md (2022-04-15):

# Klicky Probe for Ratrig VCore3 printers

Here you will find the necessary files and documentation to print and setup your own klicky probe on the VCore3 

This directory has the STL files properly oriented for printing and community mods for the respective printer, there are [klipper](../../../Klipper_macros) macros and [RRF](../../../RRF_macros) macros on the repository.

You can find more information about the RatRig printers at the [website](https://www.ratrig.com/) or go check the [discord](https://discord.gg/bxqvFH4UzW). As the main developer of this modification variant for the VCore3 I own a custom shaped VCore3 printer. These parts have however been tested now with quite a few of the standard variations sold by Ratrig.

Due to the fact there is no area on the VCore3 where the dock can be fully outside the footprint of the print bed you will lose a small amount of print volume in the very front left corner... Note the default profile uses this area for the purge line anyway and this does not need to be modified as the direction of the purge line ensure the probe is not picked up.

Above all, have fun and be excellent to one another, now to the instructions.

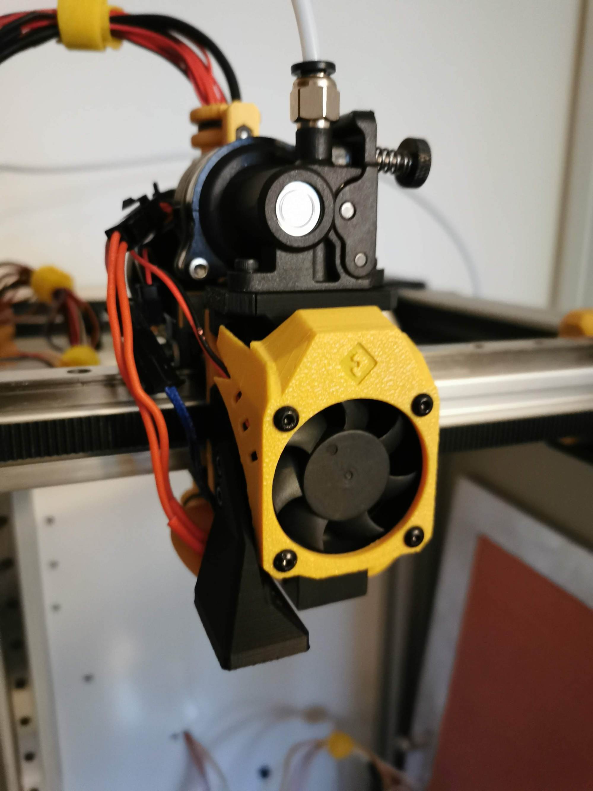
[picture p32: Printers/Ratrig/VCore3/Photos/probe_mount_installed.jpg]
V2.4 Klicky Probe


## Mounting

### Probe dock mount

The probe dock is mounted to the front left extrusion, depending on your leadscrew length some of it may poke through the hole in the bracket

### Probe toolhead mount

The probe toolhead mount has been designed to be directly compatable with the EVA system and bolts onto the probe mounting holes. (Note it does however have a different probe offset to the standard bl touch and inductive probes)

## Bill of Materials (BOM)

### Tools:

- 1.5mm Drill (optional)
- Multimeter to check for Continuity 
- Super Glue (optional but advised)
- Soldering Iron

### Probe:

- 1x microswitch (the omron D2F-5 or D2F-5L (removing the lever is required), other also work with reduced accuracy or repeatability (mostly anecdotal evidence, needs a proper sudy)
- 2x M2x10 mm self tapping
- 10cm of 22AWG cable (to wire the magnets to the switch)
- 5x 6 mm x 3 mm magnets (N35 magnets work)

### Probe mount:

- 4x 6 mm x 3 mm magnets (N35 magnets work)
- 2x 22AWG cable (to connect the Klicky Probe to the control board)
- 2x M3x6 mm BHSC Screw

### Probe dock:

- 1x 6 mm x 3 mm magnets (N35 magnets work)
- 2x M3x16 mm

### Probe dock mounts:

- 2x M6x12 cap head bolt
- 2x M3 threaded insert M3x5 mmx4 mm

## Sourcing

To get the best experience, please consider purchasing from the trusted list of suppliers bellow.

[trusted suppliers list](./Sourcing.md)

## Parts location

The probe STL's are located [here](../../../Base_STL).

The printer specific STL's are located [here](./VCore3_STL).

## What to print

- 2x KlickyProbe_v2.stl (keeping a spare is always a good idea)
- Probe_Mount_v1.stl
- Probe_Dock_v2.stl
- Probe_Dock_Mount_v1.stl

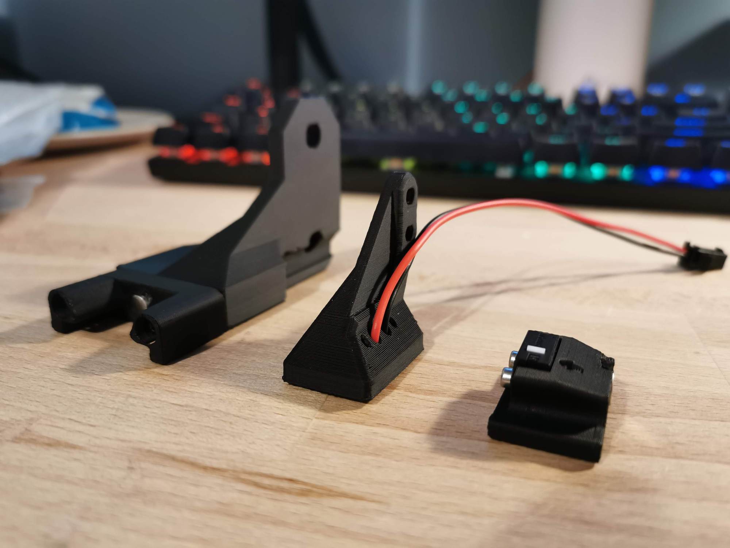
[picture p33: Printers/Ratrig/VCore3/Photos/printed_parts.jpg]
printed parts


#### Helpers to pressfit the probe magnet

- Probe_magnet_pressfit_helper.st
- Probe_magnet_holder.stl
- probe_pressfit_helper.stl

### Printing instructions

Recommended printing settings:

* initial layer height:0,24
* layer height: 0.2mm
* bottom/top/perimeters: 4
* infill: more than 23%
* infill type: Cubic
* Thin walls: On

It was tested and printed with ABS and PETG, might work on other materials, if you try, let me know how it worked out.

## Assembly

### Step 1 - Dock mount and Probe Dock assembly 

- [ ] 2x M3 threaded insert M3x5 mmx 4 mm
- [ ] 1x 6 mm x 3 mm magnets
- [ ] 2x M3x16 mm
- [ ] Super Glue

Install your heat set threaded inserts in the holes shown below.

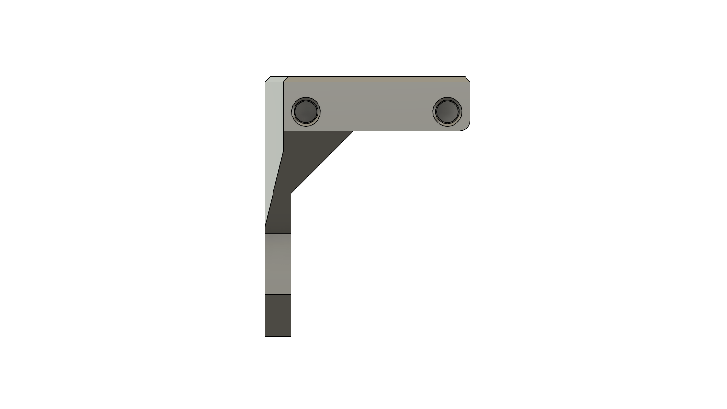
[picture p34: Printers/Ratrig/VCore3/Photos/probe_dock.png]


Install the magnet in the Probe dock, make sure that the magnet is fully inserted, it's top should be below the plastic.

Screw the dock onto the Dock mount with the two M3x16mm screws.

Secure the magnet with a dab of super glue (not a lot, just a drop).

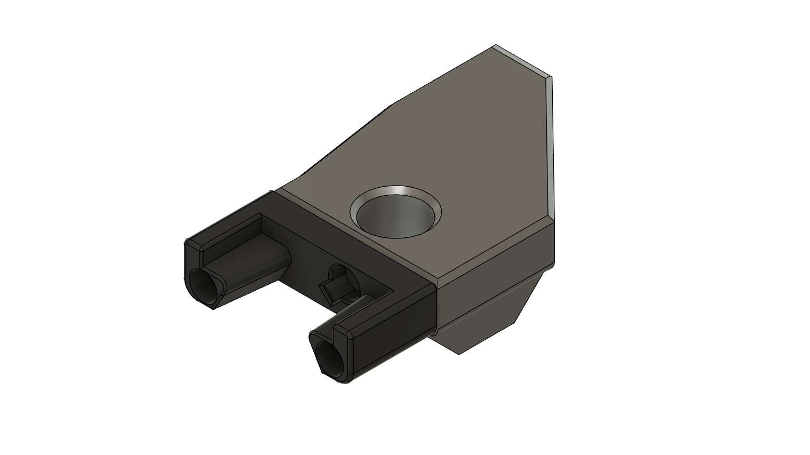
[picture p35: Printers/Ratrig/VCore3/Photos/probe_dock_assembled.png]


Mount the Probe Dock to the front left extrusion, You will adjust the Z offset in a minute.

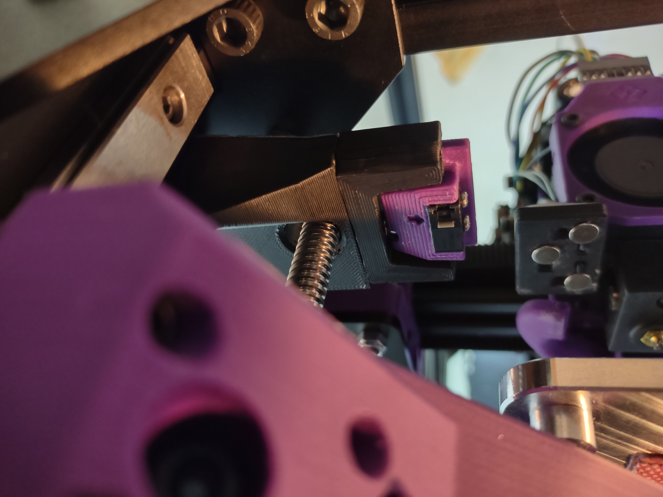
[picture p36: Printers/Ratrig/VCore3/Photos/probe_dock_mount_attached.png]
Klicky Dockmount attached


### Step 2: Probe Assembly

For the probe assembly you need the following parts:

- [ ] 1x microswitch
- [ ] 2x M2x10 mm self tapping
- [ ] 5x 6 mm x 3 mm magnets
- [ ] 22AWG cable
- [ ] 1.5mm Drill (optional)
- [ ] Multimeter to check for Continuity 
- [ ] Super Glue

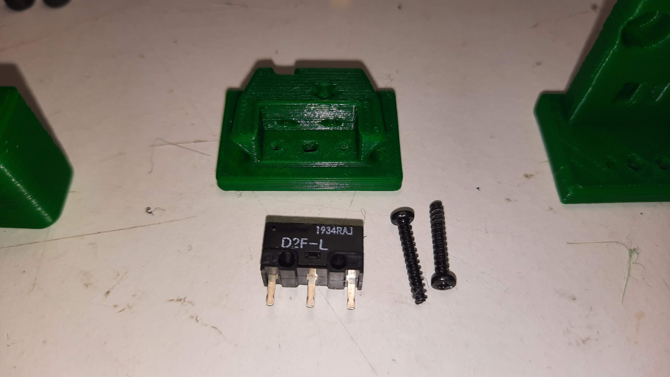
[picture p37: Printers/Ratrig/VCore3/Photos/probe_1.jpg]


Maybe you need to clear the holes for the microswitch, a 1.5mm drill bit should work fine.

Install the microswitch so that the arrow on the probe body is pointing to the little switch.

The best way to install the back magnet is to attach a magnet to the probe dock and slide the probe on the dock to insert some distance and the insert he remaining with a tool, it should be slightly below the plastic.

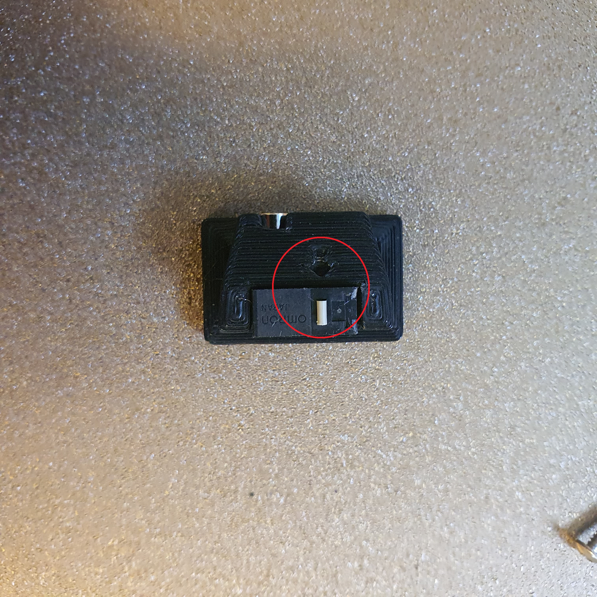
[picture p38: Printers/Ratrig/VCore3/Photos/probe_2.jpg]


Then take your self tapping screws and screw the microswitch in place, you should also now solder the wires to the outside pins of the switch, that way making this a Normally Connected probe.

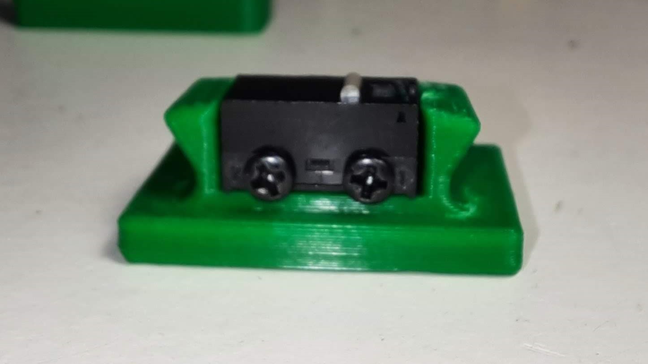
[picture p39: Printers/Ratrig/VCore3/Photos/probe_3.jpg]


You want to install the magnets in the way that the ones which are connected to the microswitch, have the same polarity.

Before placing the switch magnets, use some super glue on the holes (not a lot, just a drop), avoid the wires and the top of the magnets.

The 3rd magnet should have the inverse polarity, wait until the system is complete and assembled before gluing the magnets, they might need adjustment to ensure a good fit on the mount.

You can use the included pressfit helpers to help in securing the probe when you are inserting the magnets.

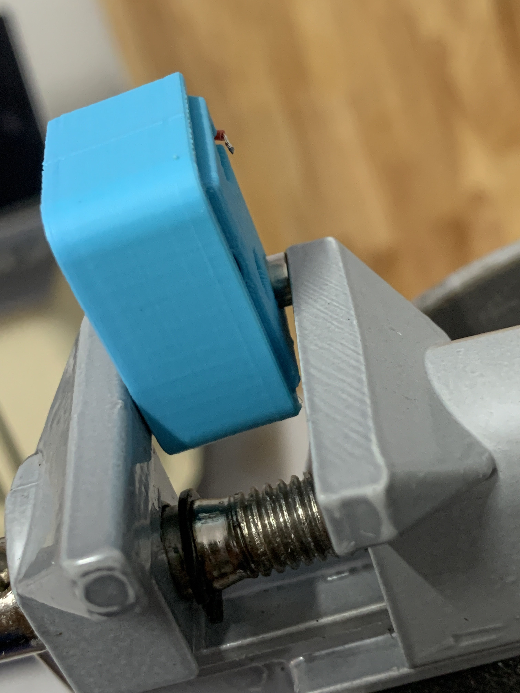
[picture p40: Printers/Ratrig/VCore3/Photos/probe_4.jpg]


There is no need for soldering, the probe microswitch connectors are press-fit on the magnets, they should remain with the top above the probe plastic.

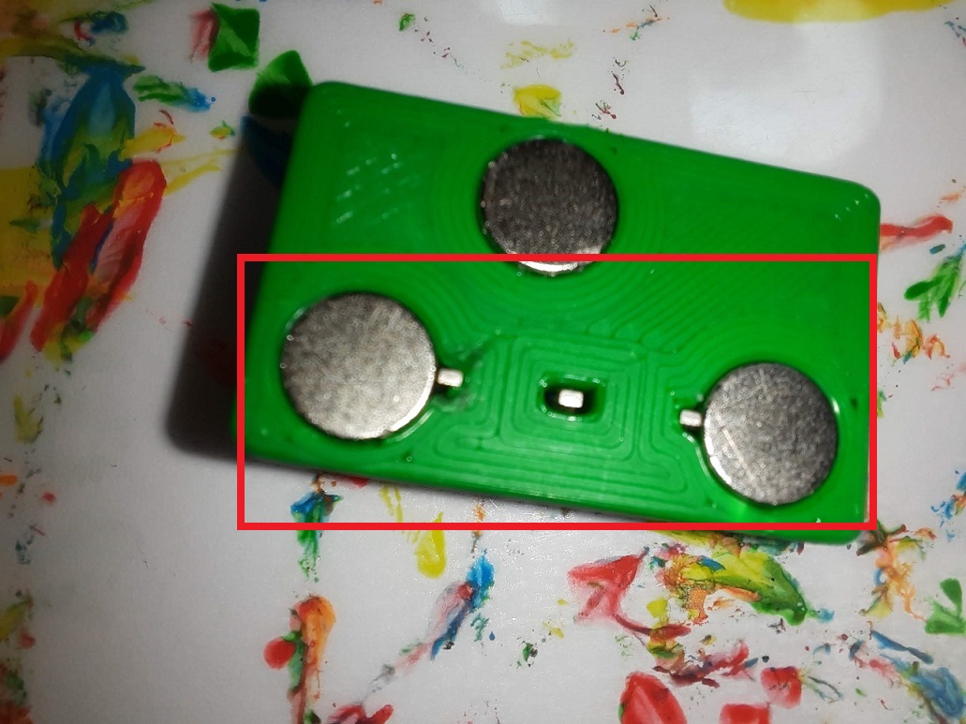
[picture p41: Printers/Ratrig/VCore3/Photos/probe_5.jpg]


As the last step of the probe assembly check if you have continuity between two magnets that connect to the switch.

If you have a normally closed switch (as you should), then you should have a current flow, so continuity is established. When you press the switch you should lose continuity. When you have a normally open switch then the behavior is the other way around.

### Step 3: Probe mount Assembly

For the probe mount assembly you need the following parts

- [ ] 3x 6 mm x 3 mm magnets
- [ ] 22AWG cable to connect the Klicky Probe
- [ ] 2x M3 x 12mm BHSC 
- [ ] Multimeter to check for Continuity 
- [ ] Super Glue

The probe mount wires are also connected with pressure from the magnets, you can use the probe magnets as a template to insert the probe mount magnets, it is easier that way, so that the magnets are not inserted the wrong way.

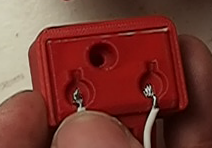
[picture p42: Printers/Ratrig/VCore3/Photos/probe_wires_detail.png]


again, before placing the wire magnets, use some super glue on the holes (not a lot, just a drop), avoid the wires and the top of the magnets.

The 3rd magnet should have the inverse polarity, exacly like on the probe.

Wait until the system is complete and assembled before gluing the 3rd magnets, they might need adjustment to ensure a good fit on the probe.

After everything is assembled let's check again for continuity, this time joining the ends of the cable and testing connectivity on the two wire magnets that have a cable.

### Step 4: Probe Mount installation and wiring

For the installation you need the following parts:

- [ ] 2x M3x12 mm BHSC Screws



Route the probe mount cables between the probe mount and the fan duct and then up the side of the EVA backplate. When installing the mount be careful not to push the hex nuts out of their grooves. It is a pain to take apart the EVA assembly to put them back in.

**Before going further, please turn off the printer, the boards are very picky with short circuits.**

Connect the probe to the controller board. You may also put an inline connector (I chose to do this) to enable easier switching in the future.

When testing the docking and attachment of the probe, make sure that the back magnet of the probe and the dock magnet do not touch, if they do, it will make attaching the probe much harder.

### Step 5: klipper configuration

As of right now, klipper and RRF have no inbuilt support for a removable probe, fortunately, it does support very robust macro programming, so you will need to add macros to be able to dock and attach the probe as necessary, as well as supporting the rest of the functions that require the usage of a probe.

The macros and instructions on how to configure are located on the [Macro directory](../../../Klipper_macros), you need to **check that before continuing on the build**, there are also some [RRF scripts](../../RRF_macros) that work.

This guide will assume users are using RATOS for their printer. It is probably easier to follow the generic Voron installation instructions if using a standard klipper installation.

Add all the klicky macros to the config directory (same level as your printer.cfg file.)

Update printer.cfg with the following changes:

Add the include line for the klicky probe

```python
#############################################################################################################
### HOMING
### Pick your probe and endstops
#############################################################################################################
# BL Touch
#[include config/z-probe/bltouch.cfg]
# Inductive/Capacitive probe
[include config/z-probe/probe.cfg]
[include klicky-probe.cfg]
```

Comment out the bltouch line if using and uncomment the probe line. Add line specifying that the probe is now connector to the z endstop pin (check your boards pinout to get the pin number). Comment out the whole safe z homing section

```python
# Z Probe configuration
#[bltouch]
#z_offset: 0.0 # Adjust this to fit your setup
[probe]
#z_offset: 0.0 # Adjust this to fit your setup
pin=PG10 # Added because using Z endstop pin as probe pin
#pin: ^probe_pin # For NPN NC probes such as the Super Pinda / Vinda / SupCR / Decoprobe probes.
#pin: ^!probe_pin # NPN NO (refer to the specs on your probe)
#pin: probe_pin # PNP NO (refer to the specs on your probe)
#pin: !probe_pin # PNP NC (refer to the specs on your probe)

# Safe Z Home (Physical endstops only)
#[safe_z_home]
#home_xy_position: 150,150 # 300mm printer
#home_xy_position: 200,200 # 400mm printer
#home_xy_position: 250,250 # 500mm printer
```
In the user overides section add the following section.

```python
[probe]
x_offset: -24.526
y_offset: -20.725
```

#### Assembled Klicky Probe

See assembled probe in action on youtube [here](https://youtu.be/aWnHNNrViP0)

### Step 6: klipper  Dock/Undock  configuration

#### Adjust Probe Pickup Position

One of the last things we need to do is to adjust the probe pickup position. I suggested manually moving the print head into position and use that to set your probe dock mount z height on the extrusion.

Turn your printer on and then make sure that the x and y axis are homed and the probe is manually attached to mount.

Now manually (with gcode commands) move the toolhead to the probe dock and move it so far to the back that the probe docks, note the Y-Position.

Next, again manually, move the toolhead parallel to the probe dock until the probe it is perfectly aligned with the mount, note the X.Position.

Open your `klicky-variables.cfg` and find the `#dock location` section and edit the following two line

```python
variable_docklocation_x:
variable_docklocation_y:
```

Test now with the ATTACH_PROBE and DOCK_PROBE if it docks and is removed correctly, some common points that can give problems are:

* the dock magnet is touching the back probe magnet, they cannot touch, push them further in
* the probe is hitting the dock arms, please move the toolhead more to the side where the probe does not hit, by 1mm at a time, until it works
* the probe is falling after being release, the dock is too far away, you can insert one or several 1mm spacer to move the dock and solve this

***WARNING when you are doing PROBE_ACCURACY, make sure that the probe is above the bed, the PROBE_ACCURACY macro does not move the toolhead in X or Y.***

Congratulations, your done :).

## Firsts tests

Before starting to test klicky, and from past mistakes, please remove your PEI sheet (the probe works on the magnetic sheet) and if possible, change your printer maximum speed, acceleration and Z current, on klipper with TMC steppers, you can do this:

```python
SET_TMC_CURRENT STEPPER=stepper_z CURRENT=0.2 
SET_VELOCITY_LIMIT ACCEL=1000
SET_VELOCITY_LIMIT VELOCITY=50
```

Enjoy your Klicky Probe!

## Dock and undock video

https://youtu.be/qqRuQJcBS7o

It is working very well, if you decide to use it, give me feedback, either here, or on discord, my discord user is Slzer#2881. Also a massive shoutout to JosAr#0517 who create the Klicky, all I did was modify it for the VCore3.

For help using or installing Klicky take a look at the guides posted on my blog [3DPandME](https://www.3dpandme.com/) or join the [discord](https://discord.gg/kKj9epxn7B) 

By standing on the shoulders of giants, lets see if we can see further.

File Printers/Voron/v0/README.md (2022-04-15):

# Klicky Probe for  Vorondesign v0 printers

Here you will find the necessary files and documentation to print and setup your own klicky probe on the v0 (and v0.1)

This directory has the STL files properly oriented for printing and community mods for the respective printer, there are [klipper](../../../Klipper_macros) macros and [RRF](../../../RRF_macros) macros on the repository.

You can find more information about the Voron printers at the [website](https://vorondesign.com/) or go check the [discord](https://discord.gg/voron), for the record, i own a v2.4, this is how i would describe them "A Voron is a fast high quality printer, i print with much better quality  the perimeters at the draft speed of my old bedslinger. It also has a  big community with lots of documentation and new ideas."

With an integrated mount, the bed can be fully used during printing, the bed only cannot be probed (at most) 6mm on the left side, this is due to the design of the probe, that extends below the nozzle.

There are currently two other probes available to use on the V0.1, Slideswipe and Sideswipe.

Above all, have fun and be excellent to one another, now to the instructions.

This mod is not yet on [VoronUsers repository](https://github.com/VoronDesign/VoronUsers/tree/master/printer_mods/JosAr/Klicky-Probe), should be soon. 

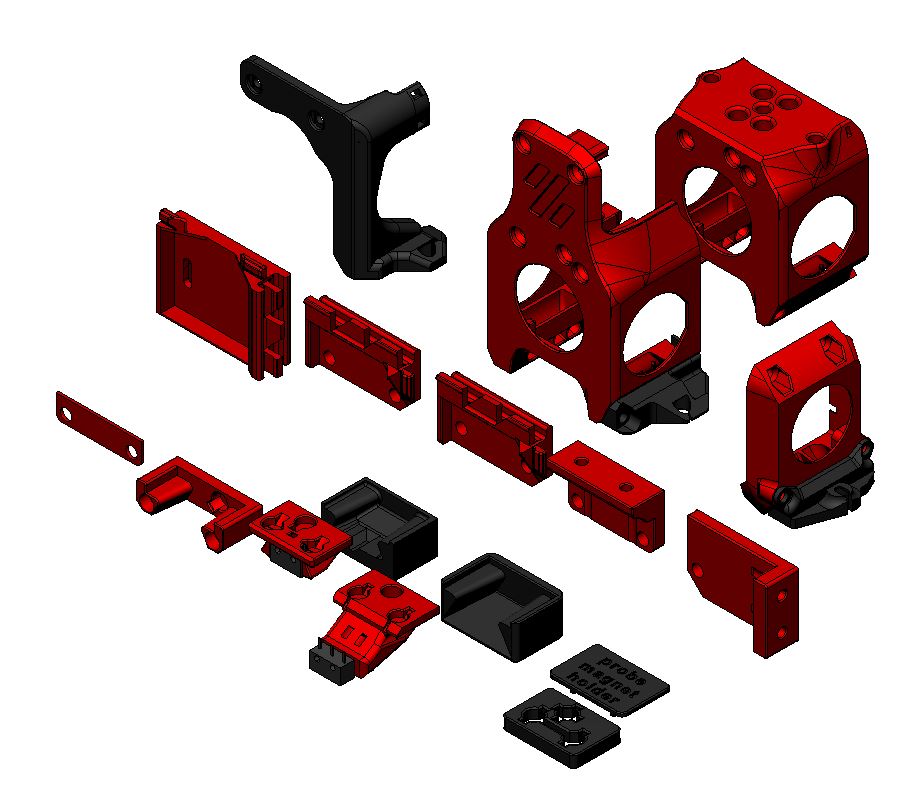
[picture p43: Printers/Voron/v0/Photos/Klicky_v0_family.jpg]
V2.4 Klicky Probe


## Mounting options

### Probe dock mount

The probe dock is mounted to the front right extrusion, where it minimizes the chance of being removed inadvertently during printing, like this:

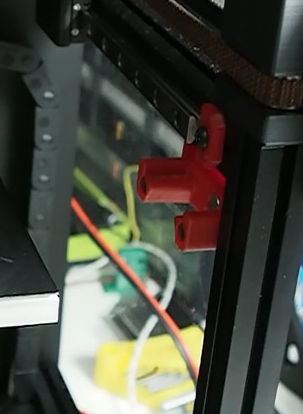
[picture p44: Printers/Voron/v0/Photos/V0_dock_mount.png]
Klicky Dockmount attached


There are several mounting options, depending on your setup:

It can be frustrating on the v0 to add extra m3 nuts on the 1515 extrusion after the assembly is complete, so there are several screwless probe dock options to avoid that scenario.

| Screwless variable | Fixed | Fixed extrabeef | Top screws | Side screws |
| :---: | :---: | :---: | :---: | :---: |
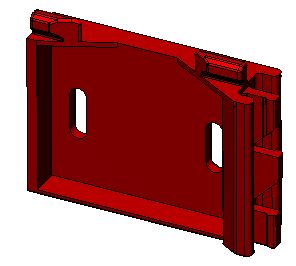
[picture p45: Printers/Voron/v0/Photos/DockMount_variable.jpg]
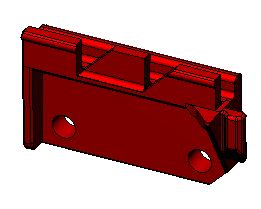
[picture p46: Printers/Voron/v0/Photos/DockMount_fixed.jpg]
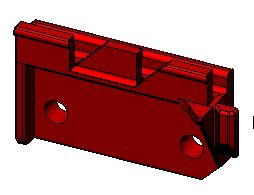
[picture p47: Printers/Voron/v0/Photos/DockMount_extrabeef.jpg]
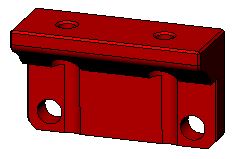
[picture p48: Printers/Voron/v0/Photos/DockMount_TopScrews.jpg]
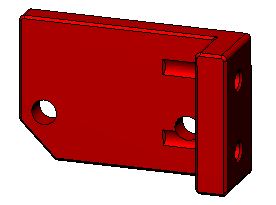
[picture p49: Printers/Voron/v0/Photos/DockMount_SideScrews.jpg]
|  |  |  |  |  |
| recommended for most setups, does not require extra m3 nuts on the extrusion (v0.0/1) | fixed position, does not require extra m3 nuts on the extrusion (v0.1) | fixed, fits X carriages that are 2mm thicker, does not require extra m3 nuts on the extrusion(v0.1) | fixed, requires 2 extra m3 nuts on the top extrusion (v0.1) | fixed, requires 2 extra m3 nuts on the front extrusion (v0.1) |

There are also some more mounting options on [Usermods](./Usermods/), like a servo powered dock. ***Check it out***

### Probe toolhead mount

The v0 toolhead was not designed to use a probe, so there is no inbuilt location to add one, so i designed two options for the v0.1 variant and one for the original v0.

#### Front cowling mount (v0.1)

You can install a mount the attaches to the front of the toolhead cowling, it will need 2/3mm of X space on the front right of the bed to avoid picking the probe up by accident, it is very easy to install, it's ideal to test the concept of probing on the v0.1

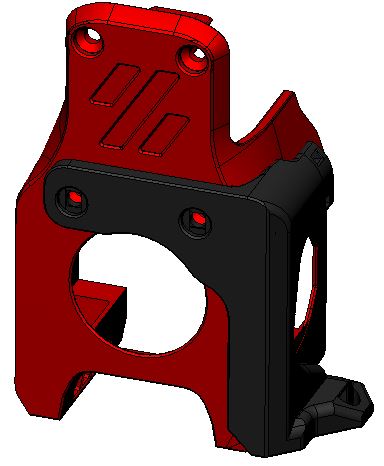
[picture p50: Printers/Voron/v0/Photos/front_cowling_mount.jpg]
Front cowling mount
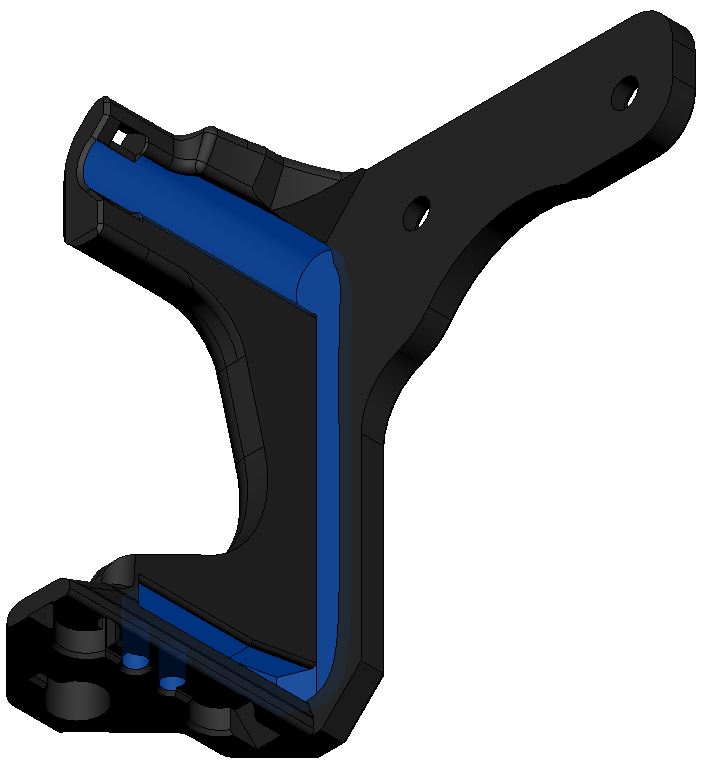
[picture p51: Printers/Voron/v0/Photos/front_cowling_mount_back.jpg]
Front cowling mount
|  |  |
| --- | --- |

You will require 2x M3 x 40mm (BHSC preferably) that are not on the V0(.1) BOM, there is an included wire path with zip tie support, to keep your printer looking good.

#### Integrated cowling (v0.1)

You can replace the cowling with a version that has a cutout to allow the klicky mount to attach, it has no impact on the cooling performance of the probe, it also includes a wire path to the back of the miniAB.

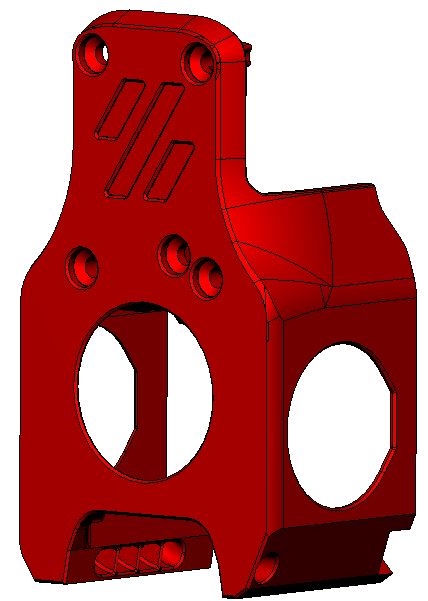
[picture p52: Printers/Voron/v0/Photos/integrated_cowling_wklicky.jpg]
Integrated klicky cowling
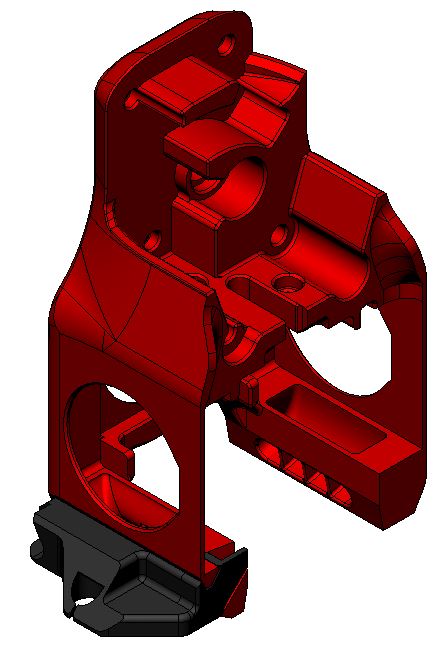
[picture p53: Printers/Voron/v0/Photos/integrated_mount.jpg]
Klicky mount
|  |  |
| --- | --- |

This method allow mounting of different probes on the V0.1, currently only klicky uses this mount, hopefully that can change in the future.

It also allows to pick up the probe at X121, effectively outside the bed, incurring in a no print space lost.

#### Fan duct mount (v0.0)

On the V0.0, you do not need to reprint the entire cowlink, you only need to replace the right fan duct with a version that has a mount for klicky, it has no impact on the cooling performance of the probe, it also includes a wire path to the back of the miniAB.

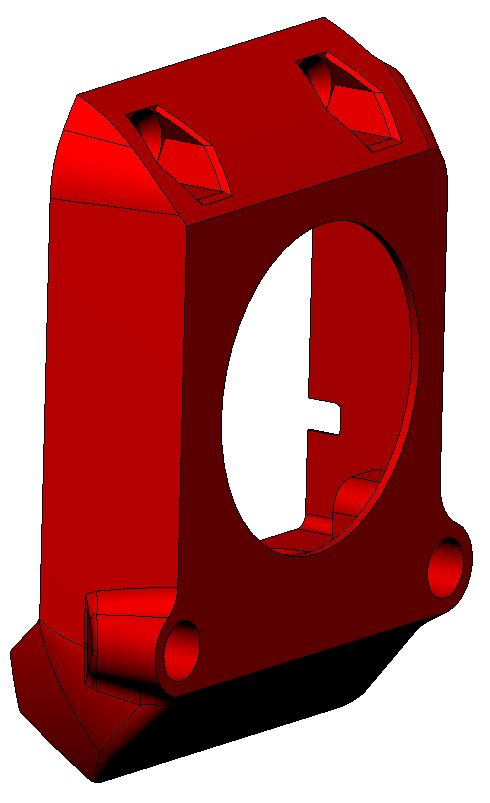
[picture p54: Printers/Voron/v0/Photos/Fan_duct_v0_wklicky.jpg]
V0 fan duct
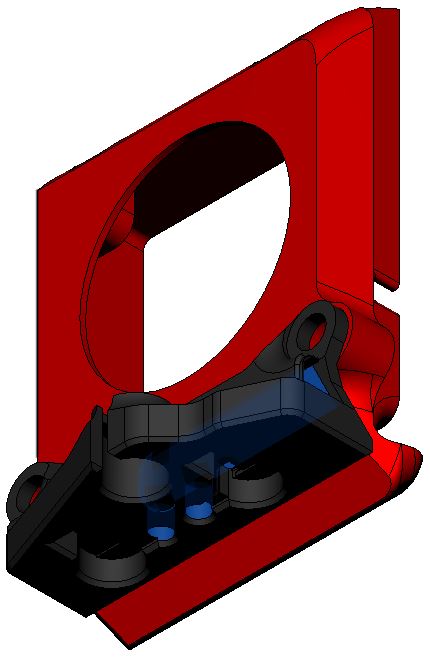
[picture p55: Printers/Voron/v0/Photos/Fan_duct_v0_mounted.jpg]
Klicky
|  |  |
| --- | --- |

This version has seen little tests because of the lack of a sufficient number of v0.0 to test on.

If you end up using this version, please tell me at what X do you dock and attach the probe.

It is also necessary to use the Screwless variable dock mount 

## Bill of Materials (BOM)

### Tools:

- 1.5mm Drill (optional)
- Multimeter to check for Continuity 
- Super Glue (optional)
- Soldering Iron

### Probe:

- 1x microswitch (the omron D2F-5 or D2F-5L (removing the lever is required), other also work with reduced accuracy or repeatability (mostly anecdotal evidence, needs a proper sudy)
- 2x M2x10 mm self tapping
- 10cm of 22AWG cable (to wire the magnets to the switch)
- 5x 6 mm x 3 mm magnets (N35 magnets work)

### Probe mount:

| Front cowling mount (v0.1) | Integrated cowling mount (v0.1) | Fan duct mount (v0.0) |
| --- | --- | --- |
| 4x 6 mm x 3 mm magnets (N35 magnets work) | 4x 6 mm x 3 mm magnets (N35 magnets work) | 4x 6 mm x 3 mm magnets (N35 magnets work) |
| 2x 20cm 22AWG cable (to connect the Klicky Probe to the umbilical termination point) | 2x 20cm 22AWG cable (to connect the Klicky Probe to the umbilical termination point) | 2x 20cm 22AWG cable (to connect the Klicky Probe to the umbilical termination point) |
| two wires to connect the controller to the extruder motor vicinity | two wires to connect the controller to the extruder motor vicinity | two wires to connect the controller to the extruder motor vicinity |
| 2x M3 x 40mm BHSC | 1x M3x6 mm BHSC Screw | 1x M3x6 mm BHSC Screw |
| | 1x M3 threaded insert M3x5 mmx4 mm | 2x M3 threaded insert M3x5 mmx4 mm |

### Probe dock:

- 1x 6 mm x 3 mm magnets (N35 magnets work)
- 2x M3x16 mm

### Probe dock mounts:

| Screwless variable (v0.0/1) | Fixed (v0.1) | Fixed extrabeef (v0.1) | Top screws (v0.1) | Side screws (v0.1) |
| :---: | :---: | :---: | :---: | :---: |
| 2x m3 nut | 2x M3 threaded insert M3x5 mmx4 mm | 2x M3 threaded insert M3x5 mmx4 mm | 2x M3 threaded insert M3x5 mmx4 mm | 2x M3 threaded insert M3x5 mmx4 mm |
| | | | 2x m3x8 mm | 2x m3x8 mm |

## Sourcing

To get the best experience, please consider purchasing from the trusted list of suppliers bellow.

[trusted suppliers list](./Sourcing.md)

## Parts location

The probe STL's are located [here](../../../Base_STL).

The printer specific STL's are located [here](./v0_STL).

The CAD with all the parts are [here](../../../CAD).

## What to print

### Probe 

* 2x KlickyProbe_Long_v2.stl (keeping a spare is always a good idea)

The KlickyProbe_v2.stl is also compatible, but has a different Y offset and cannot probe all the bed.

#### Helpers to pressfit the probe magnet

* Probe_magnet_pressfit_helper.stl

* Probe_magnet_holder.stl

* Longer_probe_pressfit_helper.stl

### Probe mount

| Front cowling mount (v0.1) | Integrated cowling mount (v0.1) | Fan duct mount (v0.0) |
| --- | --- | --- |
| Front_cowling_mount.stl | MiniAB_Dragon_Cowling_wKlicky.stl | V0_Fan_duct_wKlicky.stl |
| v0.1_integrated_mount.stl  | v0.1_integrated_mount.stl | v0_integrated_mount.stl |

There are also other integrated cowlings, check the [STL] folder, namely, the Serpa_Mini_Dragon_Cowling_wKlicky.stl from [Kyrios](https://github.com/KurioHonoo/Mini-AfterSherpa) and the LGX Lite cowling from [Bondtech](https://www.bondtech.se/2021/12/27/voron-v0-1-toolhead-setup-for-lgx-lite/).

### Probe dock

* Probe_Dock_v2.stl

### Probe dock mounts

| Screwless variable (v0.0/1) | Fixed (v0.1) | Fixed extrabeef (v0.1)  | Top screws (v0.1) | Side screws (v0.1) |
| --- | --- | --- | --- | --- |
| DockMount_variable.stl | DockMount_fixed.stl | DockMount_extrabeef.stl | DockMount_TopScrews.stl | DockMount_SideScrews.stl |

### Printing instructions

Recommended printing settings:

* initial layer height:0,24
* layer height: 0.2mm
* bottom/top/perimeters: 4
* infill: more than 23%
* infill type: Cubic
* Thin walls: On

It was tested and printed with ABS, might work on other materials, if you try, let me know how it worked out.

### Typical V0.1 components

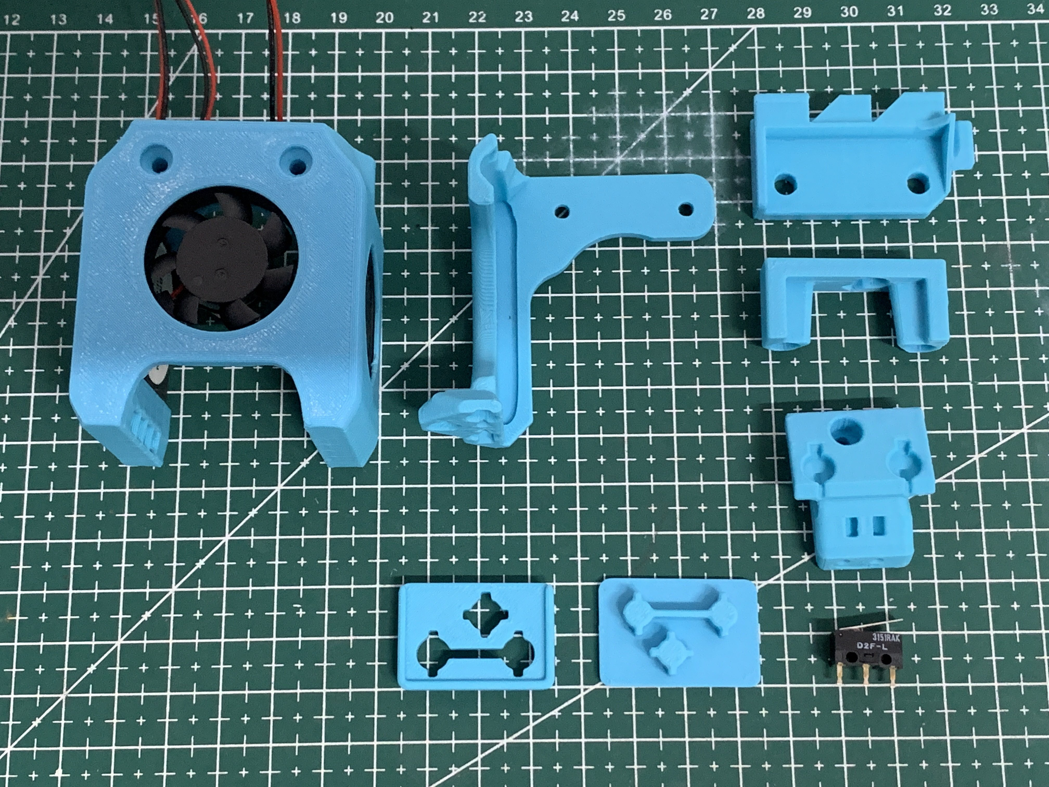
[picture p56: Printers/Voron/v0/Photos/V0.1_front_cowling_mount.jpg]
Klicky v0.1 components


(the images with the green background were provided by user SunB#1489 and are being used with permission).

## Assembly

### Step 1 - Dock mount and Probe Dock assembly 

In this examples, the Fixed dock will be used.

- [ ] 2x M3 threaded insert M3x5 mmx 4 mm
- [ ] 1x 6 mm x 3 mm magnets
- [ ] 2x M3x16 mm
- [ ] Super Glue

Here we will use the Fixed dock as an example, the other docks are very similar.

Install your heat set threaded inserts like you did within your Voron build. 

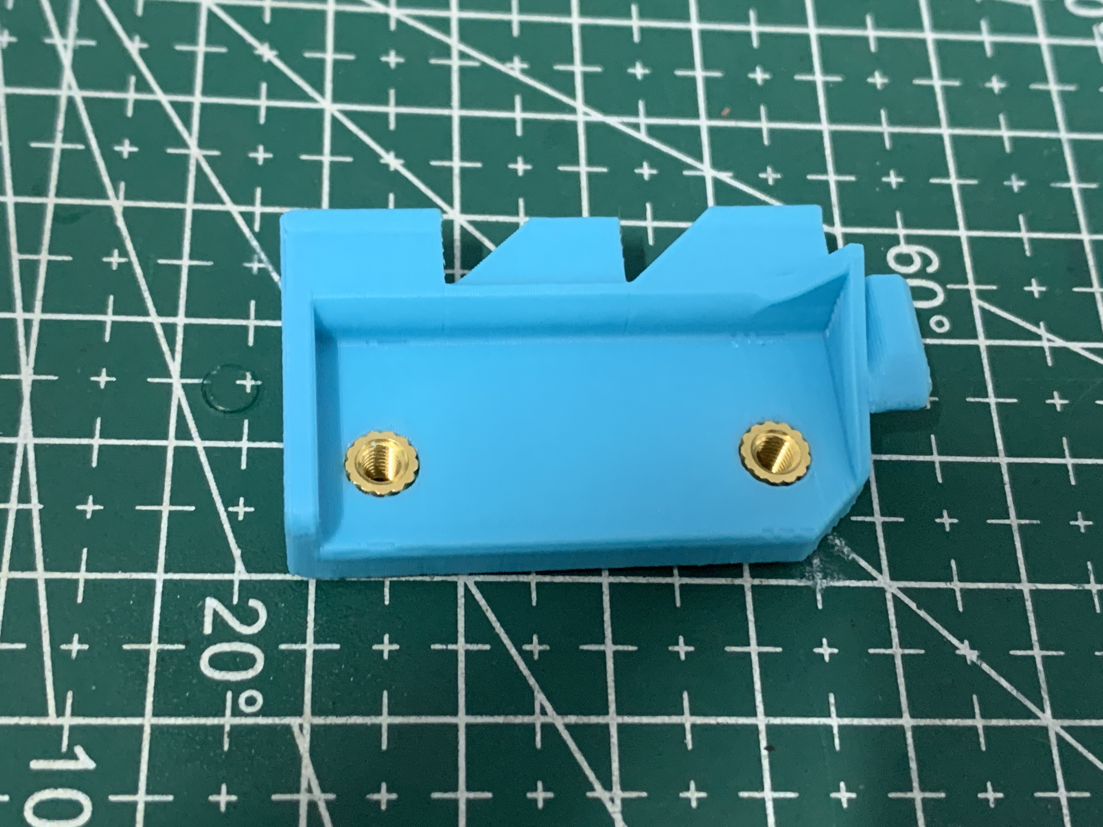
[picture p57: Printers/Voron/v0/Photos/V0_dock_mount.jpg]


Install the magnet in the Probe dock, make sure that the magnet is fully inserted, it's top should be below the plastic.

Screw the dock onto the Dock mount with the two M3x16mm screws.

Secure the magnet with a dab of super glue (not a lot, just a drop).

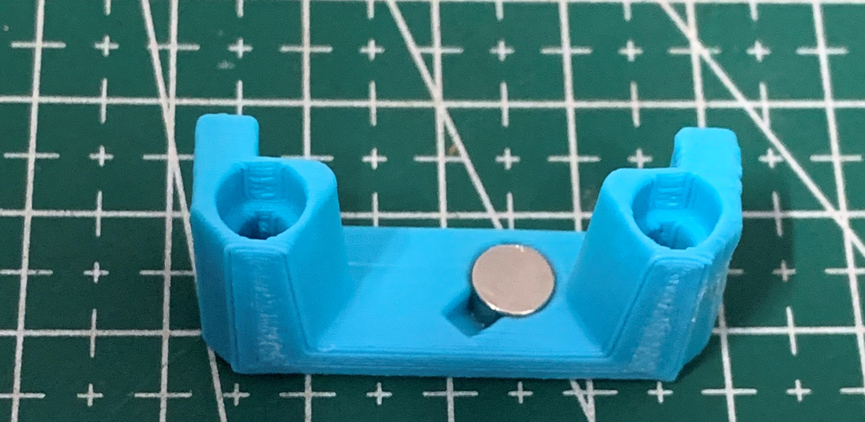
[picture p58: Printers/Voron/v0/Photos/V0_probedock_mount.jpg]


Mount the Probe Dock to the front right extrusion, snap first on the front extrusion, then on the top one (do this after assembling the probe).

Klicky Dockmount attached

### Step 2: Probe Assembly

For the probe assembly you need the following parts:

- [ ] 1x microswitch
- [ ] 2x M2x10 mm self tapping
- [ ] 5x 6 mm x 3 mm magnets
- [ ] 10cm of 22AWG cable
- [ ] 1.5mm Drill (optional)
- [ ] Multimeter to check for Continuity 
- [ ] Super Glue

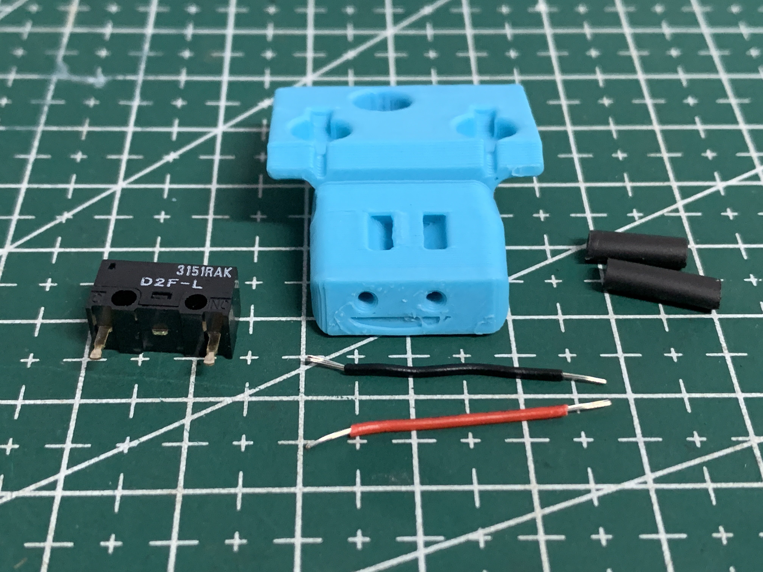
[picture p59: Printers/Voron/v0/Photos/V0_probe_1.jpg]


Maybe you need to clear the holes for the microswitch, a 1.5mm drill bit should work fine.

Install the microswitch so that the arrow on the probe body is pointing to the little switch.

The best way to install the back magnet is to attach a magnet to the probe dock and slide the probe on the dock to insert some distance and the insert he remaining with a tool, it should be slightly below the plastic.

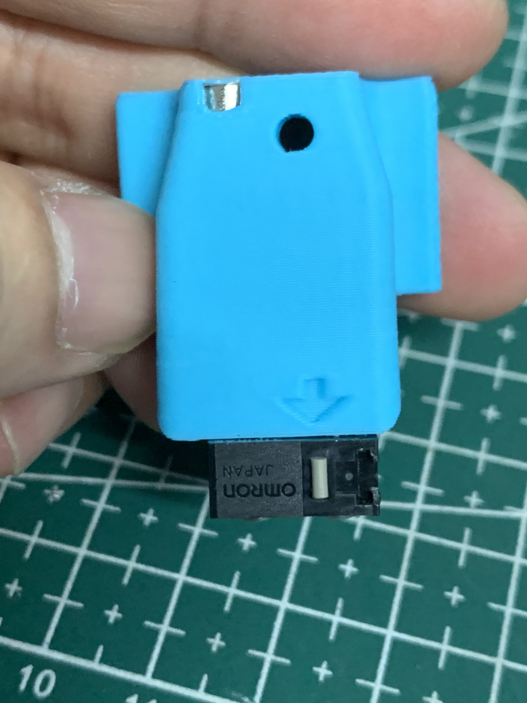
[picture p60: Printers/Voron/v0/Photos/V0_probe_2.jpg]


Then take your self tapping screws and screw the microswitch in place, you should also now solder the wires to the outside pins of the switch, that way making this a Normally Connected probe.

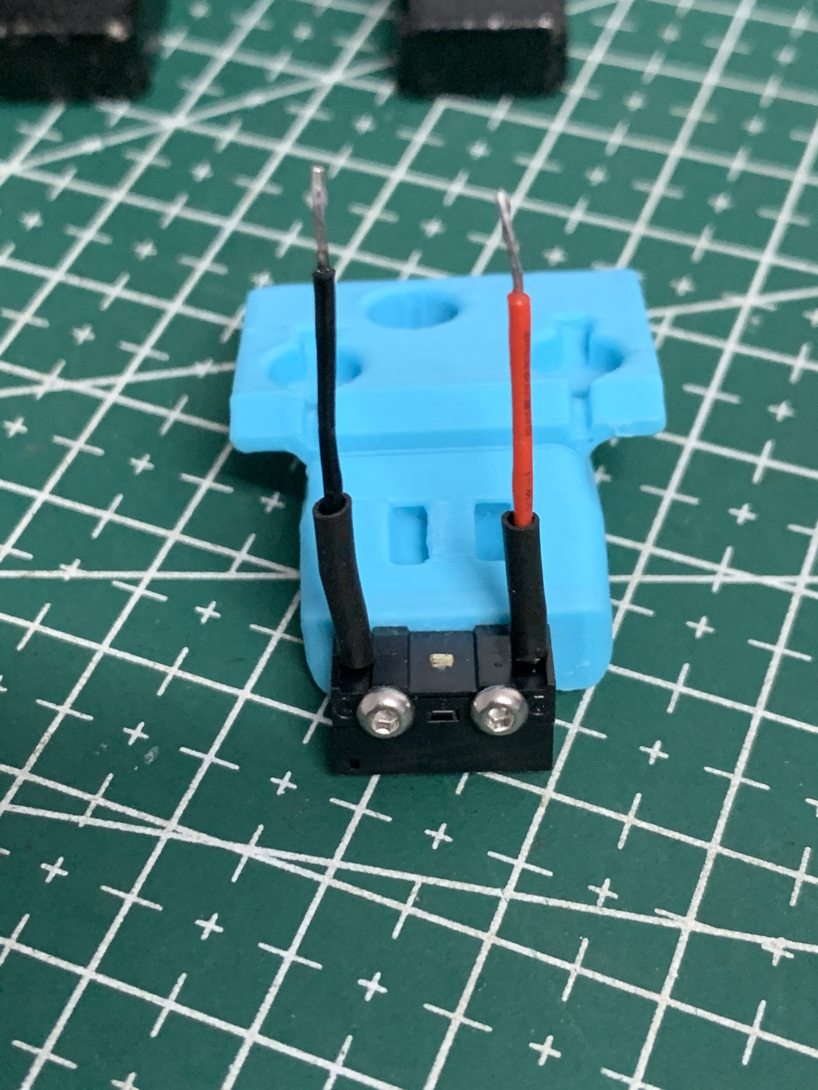
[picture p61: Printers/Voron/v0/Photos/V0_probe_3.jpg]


You should place the wires cover outside the ducts to the magnets and install them in the space below the magnets, more like the right wire is on the image below.



You want to install the magnets in the way that the ones which are connected to the microswitch, have the same polarity.

Before placing the switch magnets, use some super glue on the holes (not a lot, just a drop), avoid the wires and the top of the magnets.

The 3rd magnets (there are two) should have the inverse polarity, wait until the system is complete and assembled before gluing the magnets, they might need adjustment to ensure a good fit on the mount.

You can use the included pressfit helpers to help in securing the probe when you are inserting the magnets.



There is no need for soldering, the probe microswitch connectors are press-fit on the magnets, they should remain with the top above the probe plastic.

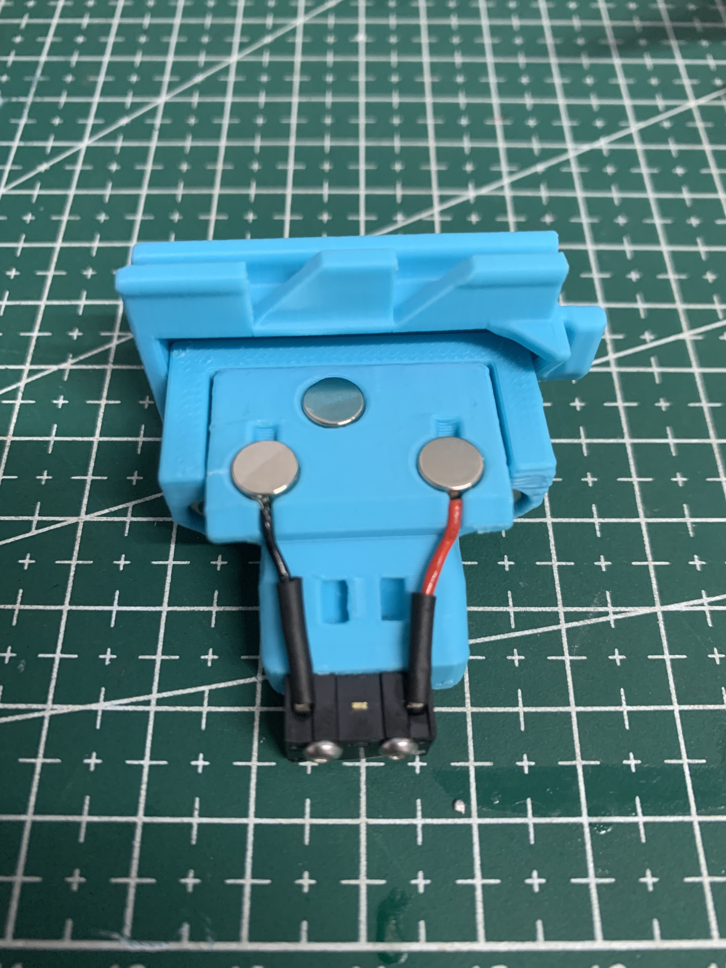
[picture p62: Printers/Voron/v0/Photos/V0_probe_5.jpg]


As the last step of the probe assembly check if you have continuity between two magnets that connect to the switch.

If you have a normally closed switch (as you should), then you should have a current flow, so continuity is established. When you press the switch you should lose continuity. When you have a normally open switch then the behavior is the other way around.

### Step 3: Probe mount Assembly

In this example, the Front cowling mount will be used.

For the Front cowling mount assembly you need the following parts

- [ ] 4x 6 mm x 3 mm magnets
- [ ] 2 x 20cm 22AWG cable to connect the Klicky Probe to the Mircofit Terminal
- [ ] two wires to connect the controller to the extruder motor vicinity
- [ ] some microfit or jst hardware
- [ ] 2x M3 x 40mm BHSC 
- [ ] Multimeter to check for Continuity 
- [ ] Super Glue

The probe mount wires are also connected with pressure from the magnets, you can use the probe magnets as a template to insert the probe mount magnets, it is easier that way, so that the magnets are not inserted the wrong way.

again, before placing the wire magnets, use some super glue on the holes (not a lot, just a drop), avoid the wires and the top of the magnets.

The 3rd magnets (there are two) should have the inverse polarity, exacly like on the probe.

Wait until the system is complete and assembled before gluing the 3rd magnets, they might need adjustment to ensure a good fit on the probe.

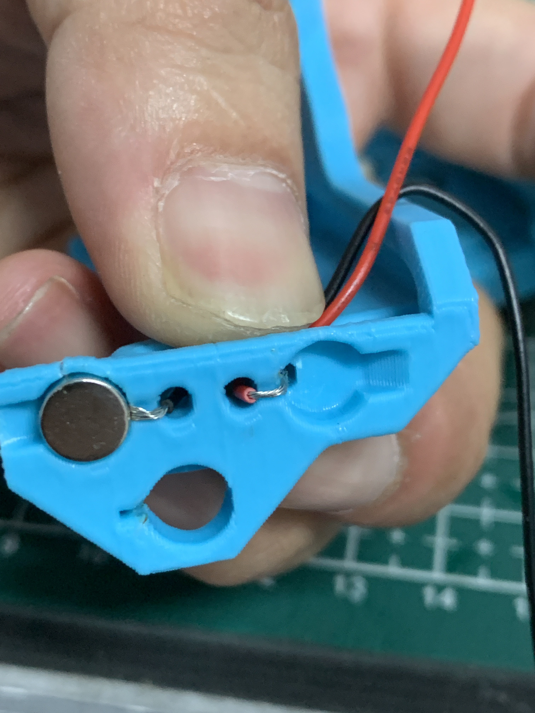
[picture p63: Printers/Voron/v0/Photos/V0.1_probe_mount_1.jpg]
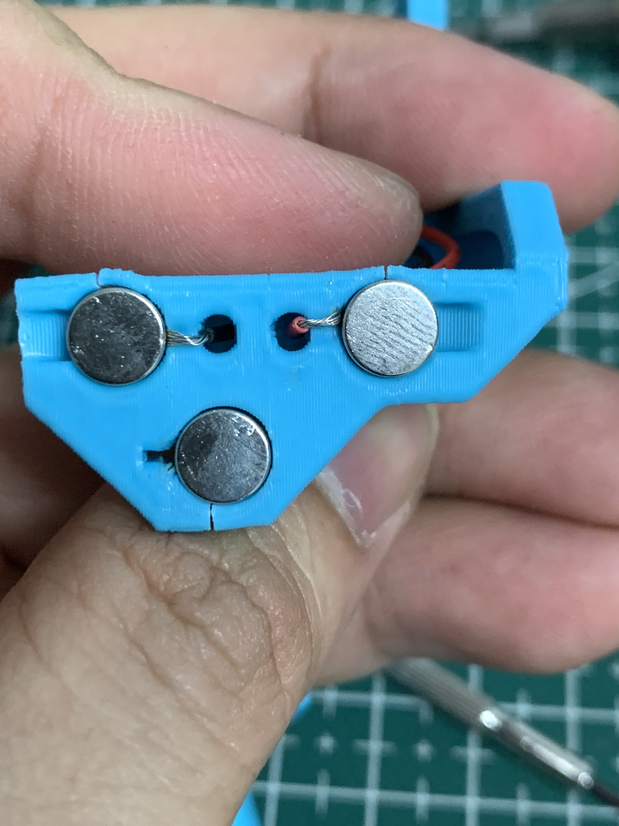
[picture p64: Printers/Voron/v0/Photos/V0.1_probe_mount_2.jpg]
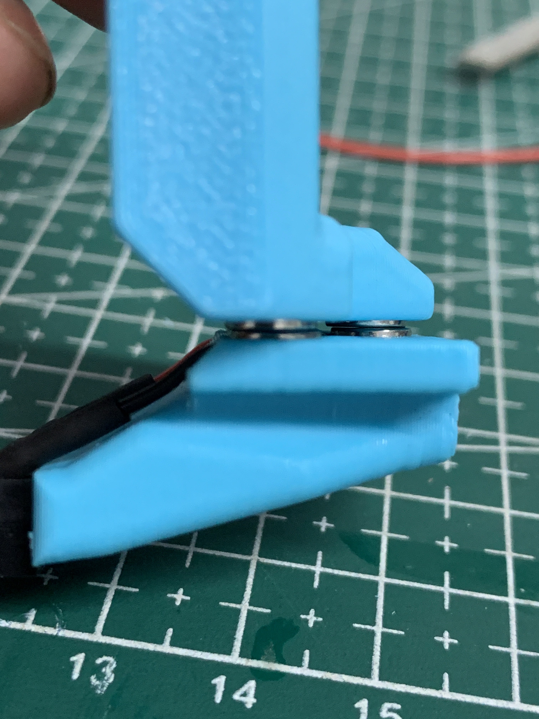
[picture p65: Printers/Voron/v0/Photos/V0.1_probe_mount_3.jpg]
|  |  |  |
| :---: | :---: | --- |

(The mount has since been improved a bit to avoid cracking)

After everything is assembled let's check again for continuity, this time joining the ends of the cable and testing connectivity on the two wire magnets that have a cable.

### Step 4: Probe Mount installation and wiring

For the installation you need the following parts:

- [ ] 2x M3x40 mm BHSC Screws

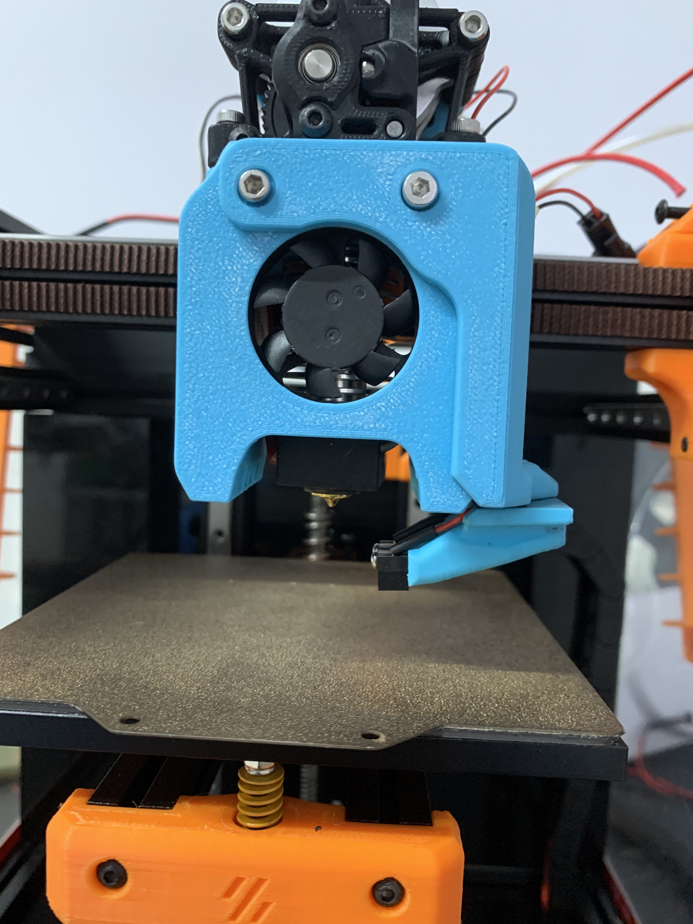
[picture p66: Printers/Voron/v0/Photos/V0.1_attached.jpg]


Route the probe mount cables to near the end of the V0 umbilical, install a male terminal in there.

**Before going further, please turn off the printer, the SKR boards are very picky with short circuits.**

Connect a female terminal to the wires that will run in the umbilical from the toolhead to the controller.

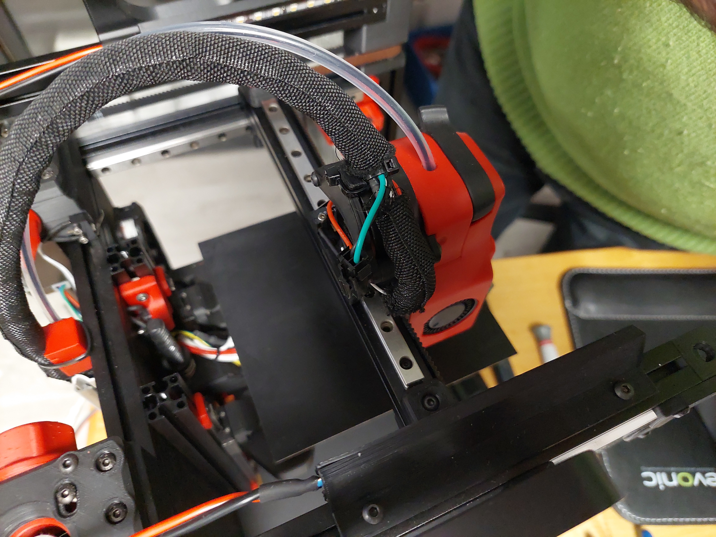
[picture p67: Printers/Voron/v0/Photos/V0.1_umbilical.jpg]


Connect the wires from the Klicky Probe to the Zprobe port, on GND and PC14 bin (I reused the LDO kit connector)

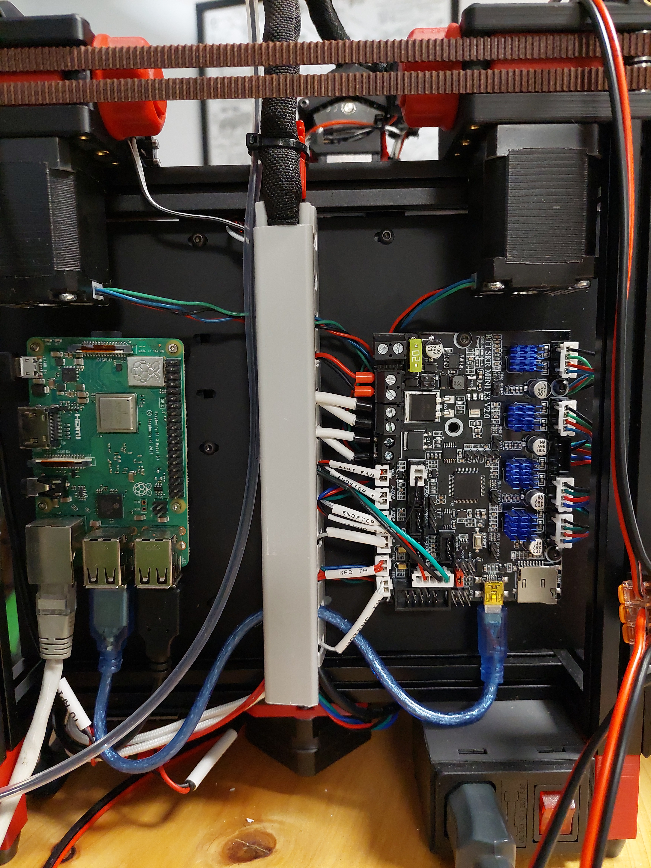
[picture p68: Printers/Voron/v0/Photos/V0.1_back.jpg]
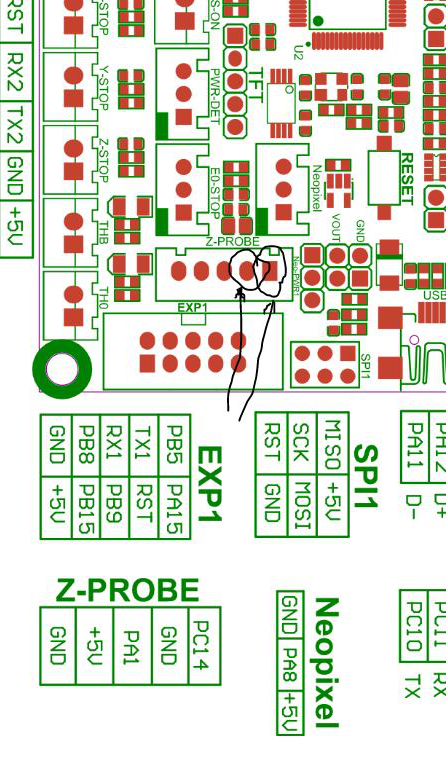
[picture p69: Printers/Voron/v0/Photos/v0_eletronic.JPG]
v0_eletronic
|  |  |
| --- | --- |

When testing the docking and attachment of the probe, make sure that the back magnet of the probe and the dock magnet do not touch, if they do, it will make attaching the probe much harder.

### Step 5: klipper configuration

Unfortunately, I do not know how to document RRF probe configuration, so here is only Klipper configurations.

As of right now, klipper and RRF have no inbuilt support for a removable probe, fortunately, it does support very robust macro programming, so you will need to add macros to be able to dock and attach the probe as necessary, as well as supporting the rest of the functions that require the usage of a probe.

The macros and instructions on how to configure are located on the [Macro directory](../../../Klipper_macros), you need to **check that before continuing on the build**, there are also some [RRF scripts](../../RRF_macros) that work for the Voron V2.4.

For the Voron v0, these are the recommended configuration on the klicky-variables.cfg:

```python
variable_verbose:               True  # Enable verbose output
variable_travel_speed:          100   # how fast all other travel moves will be performed when running these macros
variable_dock_speed:            50    # how fast should the toolhead move when docking the probe for the final movement
variable_release_speed:         55    # how fast should the toolhead move to release the hold of the magnets after docking
variable_z_drop_speed:          20    # how fast the z will lower when moving to the z location to clear the probe
    
variable_safe_z:         	    25    # Minimum Z for attach/dock and homing functions
# if true it will move the bed away from the nozzle when Z is not homed
variable_enable_z_hop:        True    # True v0
    
#Dock move
Variable_dockmove_x:             0    # Final toolhead movement to release
Variable_dockmove_y:            40    # the probe on the dock
Variable_dockmove_z:             0    # (can be negative)

#Attach move
Variable_attachmove_x:          30    # Final toolhead movement to Dock
Variable_attachmove_y:           0    # the probe on the dock
Variable_attachmove_z:           0    # (can be negative)
    
variable_max_bed_x:             120   # maximum Bed size avoids doing a probe_accuracy outside the bed
variable_max_bed_y:             120   # maximum Bed size avoids doing a probe_accuracy outside the bed

```

The sections below should be added to klicky-specific.cfg, that way, it will be loaded on klipper via a klicky-probe.cfg include.

If you would like to use a bed mesh, this is the recommended settings:

```python
[bed_mesh]
mesh_min: 15,15
mesh_max: 105,105
speed: 100
horizontal_move_z: 20 

probe_count: 3,3					#if you would like more detail, use 5,5 here
relative_reference_index: 4			 #if you use 5,5 above, place 12 here
move_check_distance: 3

algorithm: lagrange
fade_start: 1
fade_end: 10
fade_target: 0
split_delta_z: 0.0125
mesh_pps: 2,2
```

Regarding the Screws Tilt Adjust (Klipper probes the three screws positions and recommends the number of turns to level the bed), you can use this configuration as a reference, the probe should be over the screws when you do send the nozzle to the respective coordinate:

```python
[screws_tilt_adjust]
screw1: 100,115          #For Long probe
screw1_name: back right
screw2: 0,115            #For Long probe
screw2_name: back left
screw3: 60,5             #For Long probe
screw3_name: front screw
horizontal_move_z: 20
speed: 100
screw_thread: CW-M3
```

You should test this and adjust accordingly. 

This is probe configuration is with the default Voron v0.1 SKR mini E3 v2 configuration, with the probe connected to the PC14 pin, please update it to your specific configuration:

```python
[probe]
#with Long Klicky Probe
pin: ^PC14
x_offset: 8 #(9.5 with front cowling)
y_offset: 0
z_offset: 14.5
speed: 7
lift_speed: 7

samples: 3
samples_result: median
sample_retract_dist: 2

samples_tolerance: 0.01
samples_tolerance_retries: 10
```

I recommend a probing speed between 5mm/s and 10mm/s, you may experiment to see what is the better speed for your machine.
Please confirm that if you are not using a endstop pin, that the pull-up is enable by using the ^ sign, normally the endstop pins have a hardware solution that does not require this configuration.
Depending on your switch you may need to add a `!` to invert that pin (normally open vs. normally closed).

#### Z endstop and Probe configuration (virtual Z endstop)

If you want to use the Klicky Probe as your Z endstop, please read this [excellent documentation](https://github.com/T4KUUY4/Voron-Stuff/tree/main/KlickyProbeZoffset) by Takuya and Clee, as it was written for a Voron v2.4 you need to use the probe offsets that are defined in here.

#### Assembled Klicky Probe

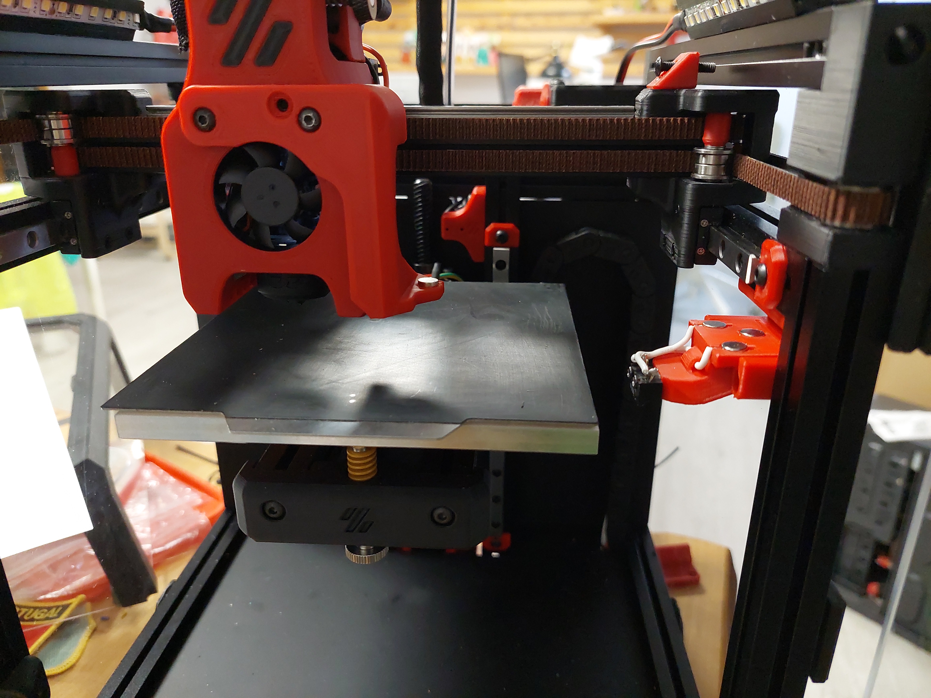
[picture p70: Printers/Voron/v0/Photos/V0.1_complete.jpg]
Assembled Klicky Probe


### Step 6: klipper  Dock/Undock  configuration
#### X max position adjustment

Even in the stock X endstop with a lever, you normally can add a extra mm of X travel due to the lever extra trigger distance:

```python
[stepper_x]
position_endstop: 120
position_max: 121
```

#### Adjust Probe Pickup Position

One of the last things we need to do is to adjust the probe pickup position.

Make sure that the x and y axis are homed and the probe is manually attached to mount.

Now manually (with gcode commands) move the toolhead to the probe dock and move it so far to the back that the probe docks, note the Y-Position.

Next, again manually, move the toolhead parallel to the probe dock until the probe it is perfectly aligned with the mount, note the X.Position.

Open your `klicky-variables.cfg` and find the `#dock location` section and edit the following two line

```python
variable_docklocation_x:
variable_docklocation_y:
```

Test now with the ATTACH_PROBE and DOCK_PROBE if it docks and is removed correctly, some common points that can give problems are:

* the dock magnet is touching the back probe magnet, they cannot touch, push them further in
* the probe is hitting the dock arms, please move the toolhead more to the side where the probe does not hit, by 1mm at a time, until it works
* the probe is falling after being release, the dock is too far away, you can insert one or several 1mm spacer to move the dock and solve this

***WARNING when you are doing PROBE_ACCURACY, make sure that the probe is above the bed, the PROBE_ACCURACY macro does not move the toolhead in X or Y.***

Congratulations, your done :).

## Firsts tests

Before starting to test klicky, and from past mistakes, please remove your PEI sheet (the probe works on the magnetic sheet) and if possible, change your printer maximum speed, acceleration and Z current, on klipper with TMC steppers, you can do this:

```python
SET_TMC_CURRENT STEPPER=stepper_z CURRENT=0.2 
SET_VELOCITY_LIMIT ACCEL=1000
SET_VELOCITY_LIMIT VELOCITY=50
```

Enjoy your Klicky Probe!

## Dock and undock video

https://youtu.be/qqRuQJcBS7o

It is working very well, if you decide to use it, give me feedback, either here, or on discord, my discord user is JosAr#0517.

By standing on the shoulders of giants, lets see if we can see further.

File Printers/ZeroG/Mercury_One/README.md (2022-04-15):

# Klicky Probe for Zero G Mercury One printers
Here you will find the necessary files and documentation to print and setup your own klicky probe on the [Zero G Mercury One](https://github.com/ZeroGDesign/Mercury).

This directory has the STL files properly oriented for printing and community mods for the respective printer, there are [klipper](../../../Klipper_macros) macros and [RRF](../../../RRF_macros) macros in the repository.

The Zero G Mercury is a Voron-inspired 3D printer conversion that turns Creality Ender 5, 5 Pro and 5 Plus machines into high-performance, klipper-based CoreXY printers.  You can find more information about the project at the [Zero G website](https://zerog.one/index.html) or the [Zero G Mercury One github](https://github.com/ZeroGDesign/Mercury), or go check their [discord](https://discord.com/invite/gzJP2s8).

## Mounting options

There are two supported gantry configurations for the Mercury One:
- *EVA*: This is the standard gantry, compatible with toolheads from the [EVA project](https://main.eva-3d.page/) project.
- *Voron Afterburner / Stealthburner*: This gantry supports the same toolheads as the Voron 2.4.

### Sourcing

To get the best experience, please consider purchasing from the trusted list of suppliers bellow.

[trusted suppliers list](./Sourcing.md)

### EVA Probe dock mount

Coming soon...

### Voron Afterburner / Stealthburner Probe dock mount

The probe dock is mounted to the rear extrusion just to the right of the leftmost Z-axis bracket:

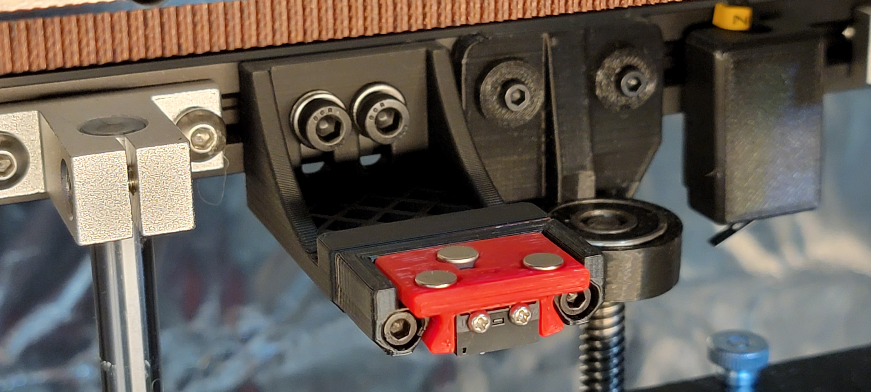
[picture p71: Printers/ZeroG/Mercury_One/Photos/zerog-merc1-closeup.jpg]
Klicky Dock Closeup

Klicky Dock Location

> Note: The dock can be mounted slightly outside of the Y-axis build volume to help avoid unintentional probe mounting while printing.  If you want to do this, you will need to adjust your Y endstop (physically) and your `[stepper_y]` `position_max` in `printer.cfg` to make sure the toolhead can reach the probe dock.

### Probe toolhead mount

The probe is mounted to the Afterburner / Stealthburner gantry bracket inside the cavity for the inductive probe. It can be used as a Z-probe for bed mesh leveling and as a Z endstop for perfect first layers on any bed.

### Printed parts
There is no need for supports, all the files are ready to print, they are in the recommended orientation.

The Klicky Probe consists of four different components:

- Toolhead components, found in the [Voron 2.4 STL directory](../../Voron/v1.8_v2.4_Legacy_Trident/v1.8_v2.4_Legacy_Trident_STL/):
    - [`KlickyProbe_AB_mount_v2.stl`](../../Voron/v1.8_v2.4_Legacy_Trident/v1.8_v2.4_Legacy_Trident_STL/KlickyProbe_AB_mount_v2.stl)
    - [`Mount_magnet_holder.stl`](../../Voron/v1.8_v2.4_Legacy_Trident/v1.8_v2.4_Legacy_Trident_STL/Mount_magnet_holder.stl)
    - [`Mount_magnet_pressfit_helper.stl`](../../Voron/v1.8_v2.4_Legacy_Trident/v1.8_v2.4_Legacy_Trident_STL/Mount_magnet_pressfit_helper.stl)
    - [`Mount_pressfit_holder.stl`](../../Voron/v1.8_v2.4_Legacy_Trident/v1.8_v2.4_Legacy_Trident_STL/Mount_pressfit_holder.stl)
- The probe itself, found in the [base STL directory](../../../Base_STL/), [KlickyProbe_v2](../../../../Base_STL/KlickyProbe_v2.stl) 
- Probe dock, found in the [base STL directory](../../../Base_STL/), [Probe_Dock_v2](../../../../Base_STL/Probe_Dock_v2.stl) 
- Frame dock mount from the [Voron_Toolhead_STL](./Voron_Toolhead_STL/) folder ([CAD models](./Voron_Toolhead_CAD/) are also available)

The recommended printing configuration is:

* initial layer height: 0.24
* layer height: 0.2mm
* bottom/top/perimeters: 4
* infill: more than 23%
* infill type: Cubic
* Thin walls: On

## Assembly

### Steps 1 through 4
Follow assembly steps 1 through 4 in the [Voron 2.4 instructions](/../../Voron/v1.8_v2.4_Legacy_Trident#assembly).

Make sure to print and use the dock mount in [Voron_Toolhead_STL](./Voron_Toolhead_STL) and install the heat set inserts:



### Step 5: klipper configuration

Unfortunately, I do not know how to document RRF probe configuration, so here is only Klipper configurations.

As of right now, klipper and RRF have no inbuilt support for a removable probe, fortunately, it does support very robust macro programming, so you will need to add macros to be able to dock and attach the probe as necessary, as well as supporting the rest of the functions that require the usage of a probe.

The macros and instructions on how to configure are located on the [Macro directory](../../../Klipper_macros), you need to **check that before continuing on the build**, there are also some [RRF scripts](../../RRF_macros).

For the printers that are covered here, this is the recommended configuration in `klicky-variables.cfg`:

```python
variable_verbose:               True  # Enable verbose output
variable_travel_speed:          200   # how fast all other travel moves will be performed when running these macros
variable_dock_speed:            50    # how fast should the toolhead move when docking the probe for the final movement
variable_release_speed:         75    # how fast should the toolhead move to release the hold of the magnets after docking
variable_z_drop_speed:          20    # how fast the z will lower when moving to the z location to clear the probe

variable_safe_z:         	    25    # Minimum Z for attach/dock and homing functions
# If true it will move the bed away from the nozzle when Z is not homed

variable_enable_z_hop:          True  # set this to false for beds that fall significantly under gravity (almost to Z max)

# Dock move (the final movement required to reach the dock and avoid the arms with the probe attached)
Variable_dockmove_x:            40    # Final toolhead movement to release
Variable_dockmove_y:            0     # the probe on the dock
Variable_dockmove_z:            0     # (can be negative)

# Attach move (the final movement required release the probe on the dock)
Variable_attachmove_x:          0     # Final toolhead movement to Dock
Variable_attachmove_y:          30    # the probe on the dock
Variable_attachmove_z:          0     # (can be negative)

variable_docklocation_z:      -128    # Z dock position (-128 for a gantry/frame mount)
```

This is an example `printer.cfg` configuration for a BigTreeTech Octopus Pro, with the Klicky probe connected to the `PC5` probe pin, please update it to your specific configuration.  It is recommended to set the probe voltage on the Octopus to `5v` instead of the default `24v`.  Alternatively, you can use a normal endstop pin for the Klicky probe.

```python
[probe]
pin: PC5 # Set the Octopus jumper to 5v instead of the default 24v!
x_offset: -1.5
y_offset: 19.75
z_offset: 7.450
speed: 2.5
samples: 3
samples_result: median
sample_retract_dist: 2.0
samples_tolerance: 0.01
samples_tolerance_retries: 5

[bed_mesh]
speed: 120
horizontal_move_z: 10
mesh_min: 20, 24
mesh_max: 210, 190 # Ender 5 / 5 Pro
#mesh_max: 340, 310 # Ender 5 Plus
probe_count: 5,3
```

I recommend a probing speed between 5mm/s and 10mm/s, you may experiment to see what is the better speed for your machine.
Please confirm that if you are using the probe input, that the pull-up is enable by using the ^ sign, normally the endstop pins have a hardware solution that does not require this configuration.
Depending on your switch you may need to add a `!` to invert that pin (normally open vs. normally closed).
Normally the endstop pins use a hardware solution, so it is not necessary.

There is now an arrow on the probe telling you where should the switch pole be to have the correct offset.

#### Z endstop and Probe configuration

If you want to use the Klicky Probe as your Z endstop (recommended), you need to change the `endstop_pin:` under the `[stepper_z]` section to `probe:z_virtual_endstop`.

Just comment out the old one and add a new line `endstop_pin: probe:z_virtual_endstop` and comment out `position_endstop`:

To use Klicky as a Z-endstop (recommended), you must update `printer.cfg`:
```python
[stepper_z]
endstop_pin: probe:z_virtual_endstop # Klicky probe Z endstop
#position_endstop: -0.10
```

You will need to update the `klicky-variables.cfg` Z probing variables, set the two variables below to `0`, it will probe the middle of the bed.

```python
variable_z_endstop_x:     0
variable_z_endstop_y:     0
```

#### Assembled Klicky Probe

Assembled Klicky Probe

### Step 6: klipper  Dock/Undock configuration

#### Adjust Probe Pickup Position

One of the last things we need to do is to adjust the probe pickup position.

Make sure that the x and y axis are homed and the probe is manually attached to mount, it is easier to do with the hotend and fan duct removed.

Now manually (with gcode commands) move the toolhead to the front of the probe dock, adjust X so that moving along Y does not hit the dock arms, ***note the X-Position***.

Example for a Ymax of `305`:

```gcode
G0 X20 Y270
G0 X20 Y280 (you see that the right side will hit the dock arm)
G0 X20 Y270
G0 X19 Y270
G0 X19 Y280 (still hitting the dock on the right side)
G0 X19 Y270
G0 X18 Y270
G0 X17 Y280 (now does not hit)
```
Your `variable_docklocation_x` is determined to be `17`

Now manually (with gcode commands) move the toolhead to the  X:`variable_docklocation_x`, Y:`max-40` position.
In the example above, it would be `G0 X17 Y265`.

The probe and dock magnet can be 1/2 mm away from each other, that is ok, they will attach when the probe is released from the mount.

Now move the toolhead 40mm to the side and check if the probe is docked securely.
If it does, perfect, variable_docklocation_y is your `Ymax`, if not, you need to either increase the `Ymax` or add a dock extender and repeat the process.

Open your `klicky-variables.cfg` and find the `#dock location` section and edit the following two lines

```python
variable_docklocation_x:
variable_docklocation_y:
```

Test now with the `ATTACH_PROBE` and `DOCK_PROBE` macros to see if it docks and is removed correctly, some common points that can give problems are:

* the dock magnet is touching the back probe magnet, they cannot touch, push them further in
* the probe is hitting the dock arms, please move the toolhead more to the side where the probe does not hit, by 1mm at a time, until it works
* the probe is falling after being release, the dock is too far away, you can insert one or several 1mm spacer to move the dock and solve this

#### Probe_accuracy and Probe_calibrate

> ***WARNING***: when you are doing `PROBE_ACCURACY`, make sure that the probe is above the bed, the `PROBE_ACCURACY` macro does not move the toolhead in X or Y.

## Firsts tests

Before testing klicky, and from past mistakes, please remove your PEI sheet (the probe works on the magnetic sheet) and

If possible, change your printer maximum speed, acceleration and Z current, on klipper with TMC steppers, this is how you do it:

```python
SET_TMC_CURRENT STEPPER=stepper_z CURRENT=0.6
SET_TMC_CURRENT STEPPER=stepper_z1 CURRENT=0.6
SET_TMC_CURRENT STEPPER=stepper_z2 CURRENT=0.6
SET_TMC_CURRENT STEPPER=stepper_z3 CURRENT=0.6
SET_VELOCITY_LIMIT ACCEL=1000
SET_VELOCITY_LIMIT VELOCITY=100
```

Enjoy your Klicky Probe!

## Dock, undock and Z-endstop probing video
This video shows the docking, undocking and z-endstop probing process in a Zero G Mercury One

Klicky Probe in action (https://www.youtube.com/watch?v=HXm9AFOVeQQ)

It is working very well, if you decide to use it, give me feedback, either here, or on discord, my discord user is srkthain#6222.

By standing on the shoulders of giants, lets see if we can see further.

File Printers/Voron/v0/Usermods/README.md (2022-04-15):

# V0.1 Klicky Usermods

[## Retractable Probe Dock](./KlickSwipe/) by Andre

"KlickSwipe is a alternative mount for the klicky probe derived from the [SlideSwipe](https://github.com/chestwood96/SlideSwipe/) probe, but modified specifically for Klicky."
It's designed for 1515 extrusions.

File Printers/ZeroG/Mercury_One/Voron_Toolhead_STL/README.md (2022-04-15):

# STL files for Klicky probe on a Zero G Mercury One with Voron Toolhead

Here you can find the parts that are specific to the Zero G Mercury One when using a Voron Toolhead (Afterburner / Stealthburner).

There is no need for supports, all the files are ready to print, they are in the recommended orientation.

The Klicky Probe consists on four different components:
- Toolhead mount, found on the [AB/SB STL directory](../../../Voron/v1.8_v2.4_Legacy_Trident/v1.8_v2.4_Legacy_Trident_STL) [KlickyProbe_AB_mount_v2](../../../Voron/v1.8_v2.4_Legacy_Trident/v1.8_v2.4_Legacy_Trident_STLKlickyProbe_AB_mount_v2) 
- the probe itself, found on the [base STL directory](../../../../Base_STL) [KlickyProbe_v2](../../../../Base_STL/KlickyProbe_v2.stl) 
- probe dock, found on the [base STL directory](../../../../Base_STL) [Probe_Dock_v2](../../../../Base_STL/Probe_Dock_v2.stl) 
- Frame dock mount, found in this directory.

The recommended printing configuration are:

* initial layer height: 0.24
* layer height: 0.2mm
* bottom/top/perimeters: 4
* infill: more than 23%
* infill type: Cubic
* Thin walls: On

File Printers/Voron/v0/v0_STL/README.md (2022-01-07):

# STL files for Klicky probe on a Voron v0



Here you can find the parts that are Voron v0 specific, the green part is only on the CAD files, it's used to cut cowlings to support the integrated mount.

There is no need for supports, all the files are ready to print, they are in the recommended orientation.

The Klicky Probe consists on four different components:
- Toolhead mount
- the probe itself, found on the initial STL directory
- probe dock, found on the initial STL directory
- Frame dock mount

The recommended printing configuration are:

* initial layer height: 0,24
* layer height: 0.2mm
* bottom/top/perimeters: 4
* infill: more than 23%
* infill type: Cubic
* Thin walls: On

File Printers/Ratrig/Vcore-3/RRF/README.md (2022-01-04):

These macros are not universal yet and are designed to function with my RRF configuration. They should provide a reasonable starting point to get you up and running though!

1. Place klicky_pick and klicky_place into the macros folder. You will need to change the positions and test the pick/place routine - My configuration uses 0,0 as the center of the bed.
2. Update config.g (overwrite lines related to probe definition and global variables)
3. update homez and homeall to include checks on whether to pick probe up or not
4. update mesh.g 
5. update bed.g

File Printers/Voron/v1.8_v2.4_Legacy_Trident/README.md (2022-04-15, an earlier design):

# Klicky Probe for  Vorondesign V1.8,V2.4, Legacy and Trident printers

Here you will find the necessary files and documentation to print and setup your own klicky probe.
Don't forget to download all [the necessary parts](https://github.com/jlas1/Klicky-Probe/tree/main/Printers/Voron/v1.8_v2.4_Legacy_Trident#parts-location).

This directory has the specific klipper macros (and a link to RRF scripts), STL files properly oriented for printing and community mods for the respective printer.

**This is an intermediate/advanced configuration, it's recommended to first build your Voron to the stock configuration**
That way, you will be better familiarized with the concepts that are presented here and will have a much more enjoyable experience.

You can find more information about the Voron printers at the [website](https://vorondesign.com/) or go check the [discord](https://discord.gg/voron), for the record, i own one, a v2.4, this is how i would describe them "A Voron is a fast high quality printer, i print with much better quality  the perimeters at the draft speed of my old bedslinger. It also has a  big community with lots of documentation and new ideas."

Above all, have fun and be excellent to one another, now to the instructions.

V2.4 Klicky Probe

## Mounting options

The probe dock is mounted either to the frame or to the XY gantry, allowing it to be used as a Z endstop if desired as it's Z is fixed relative to the toolhead.

There are several gantry extrusion mounts possible, all attached  between the A end B motors:

| Fixed * | Variable * | Fixed sidemount left * ** | Fixed sidemount right * ** | Legacy fixed |
| :---: | :---: | :---: | :---: | :---: |
|  |  |  |  |  |
| fixed docking position | adjustable docking position | fixed docking position, allows for purge bucket mod | fixed docking position, allows for purge bucket mod | fixed docking position (Legacy) (designed by Baltojikale) |

*usable on the V1.8, V2.4 and Trident
**attempts to put the dock to the side of the [purge bucket](https://github.com/VoronDesign/VoronUsers/tree/master/printer_mods/edwardyeeks/Decontaminator_Purge_Bucket_&_Nozzle_Scrubber), there is  [also a mod](https://github.com/Ramalama2/Voron-2-Mods/tree/main/PurgeBucket_350_Klicky) to allow the usage of the fixed dock

There are also some more mounting options on [Usermods](./Usermods/), integrated magnets in the AfterBurner toolhead and some complementary items. ***Check it out***

This mod is also on [VoronUsers repository](https://github.com/VoronDesign/VoronUsers/tree/master/printer_mods/JosAr/Klicky-Probe) 

## Bill of Materials (BOM)

### Tools:

- 1.5mm Drill (optional)
- Multimeter to check for Continuity 
- Super Glue (optional)
- Soldering Iron for the heat inserts

### Probe:

- 1x microswitch (the omron D2F-5 or D2F-5L (removing the lever is required), other also work with reduced accuracy or repeatability (mostly anecdotal evidence, needs a proper sudy)
- 2x M2x10 mm self tapping
- 4x 6 mm x 3 mm magnets (N35 magnets work)

### AB/SB mount:

- 3x 6 mm x 3 mm magnets (N35 magnets work)
- 2x M3x8 mm SHC Screws
- 2x 10cm 22AWG cable to connect the Klicky Probe to the terminal

### Probe dock:

- 1x 6 mm x 3 mm magnets (N35 magnets work)
- 2x M3x16 mm

### Probe dock mounts:

| Fixed | Variable | Fixed sidemount left | Fixed sidemount right | Legacy fixed |
| --- | --- | --- | --- | --- |
| 2x M3 threaded insert M3x5 mmx4 mm | 10x M3 threaded insert M3x5 mmx4 mm | 4x M3 threaded insert M3x5 mmx4 mm | 4x M3 threaded insert M3x5 mmx4 mm | 2x M3 threaded insert M3x5 mmx4 mm |
| 2x M5x10 mm | 2x M5x10 mm | 2x M5x10 mm | 2x M5x10 mm | 2x M5x10 mm |
| 2x M5 t-nut or equivalent | 2x M5 t-nut or equivalent | 2x M5 t-nut or equivalent | 2x M5 t-nut or equivalent | 2x M5 t-nut or equivalent |
| | 8x M3x8 mm | 2x M3x8 mm | 2x M3x8 mm | |

## Sourcing

To get the best experience, please consider purchasing from the trusted list of suppliers bellow.

[trusted suppliers list](./Sourcing.md)

## Parts location

The probe STL's are located [here](../../../Base_STL).

The printer specific STL's are located [here](./v1.8_v2.4_Legacy_Trident_STL).

The CAD with all the parts are [here](../../../CAD).

## What to print

### Probe

* 2x KlickyProbe_v2.stl (keeping a spare is always a good idea)

#### Helpers to pressfit the probe magnet

* Probe_magnet_pressfit_helper.stl

* Probe_magnet_holder.stl

* Probe_pressfit_holder.stl

### AB/SB mount

* KlickyProbe_AB_mount_v2.stl

#### Helpers to pressfit the probe magnet

* Mount_magnet_pressfit_helper.stl

* Mount_magnet_holder.stl

* Mount_pressfit_holder.stl

### Probe dock

* Probe_Dock_v2.stl

### Probe dock mounts

| Fixed | Variable | Fixed sidemount left | Fixed sidemount right | Legacy fixed |
| --- | --- | --- | --- | --- |
| Dock_mount_fixed_v2.stl | Dock_mount_variable_pt1_v2.stl | Dock_sidemount_fixed_v2.stl | Dock_sidemount_fixed_v2.stl | Legacy_dock_mount_fixed_v2.stl |
| | Dock_mount_variable_pt2_v2.stl | Dock_sidemount_left_v2 | Dock_sidemount_right_v2 | |
| | Dock_mount_variable_pt3_v2.stl | | | |
| | | | | |

### Printing instructions

Recommended printing settings:

* initial layer height:0,24
* layer height: 0.2mm
* bottom/top/perimeters: 4
* infill: more than 23%
* infill type: Cubic
* Thin walls: On

It was tested and printed with ABS, might work on other materials, if you try, let me know how it worked out.

## Assembly

### Step 1 - Dock mount and Probe Dock assembly 

- [ ] 2x M3 threaded insert M3x5 mmx 4 mm
- [ ] 2x M3x20 mm
- [ ] 2x M5x10 mm
- [ ] 2x M5 t-nut or equivalent
- [ ] 1x 6 mm x 3 mm magnets
- [ ] Super Glue

Here we will use the Fixed dock as an example, the other docks are very similar.

Install your heat set threaded inserts like you did within your Voron build. 



Install the magnet in the Probe dock, make sure that the magnet is fully inserted, it's top should be below the plastic.

Screw the dock onto the Dock mount with the two M3x20mm screws.

Secure the magnet with a dab of super glue (not a lot, just a drop).

DockMountandProbeMount

Mount the Probe Dock to the back rail of your gantry with the two M5x10 and the two roll in nuts.

### Step 2: Probe Assembly

For the probe assembly you need the following parts:

- [ ] 1x microswitch
- [ ] 2x M2x10 mm self tapping
- [ ] 4x 6 mm x 3 mm magnets
- [ ] 1.5mm Drill (optional)
- [ ] Multimeter to check for Continuity 
- [ ] Super Glue



Maybe you need to clear the holes for the microswitch, a 1.5mm drill bit should work fine.

Install the microswitch so that the arrow on the probe body is pointing to the little switch.





Then take your self tapping screws and screw the microswitch in place.



Before placing the magnets, use some super glue on the holes (not a lot, just a drop), avoid the switch parts.

You want to install the magnets in the way that the ones which are connected to the microswitch, have the same polarity  The 3rd magnet should have the inverse polarity, you can use the included pressfit helpers to help in securing the probe when you are inserting the magnets.

There is no need for soldering, the probe microswitch connectors are press-fit on the magnets, they should remain with the top above the probe plastic.



Don't forget to install the magnet which holds the probe to the probe dock, make sure it is fully inserted.

As the last step of the probe assembly check if you have continuity between these two magnets



If you have a normally closed switch (as you should), then you should have a current flow, so continuity is established. When you press the switch you should lose continuity. When you have a normally open switch then the behavior is the other way around.

### Step 3: AB/SB Mount Assembly

For the AB/SB Mount assembly you need the following parts

- [ ] 3x 6 mm x 3 mm magnets
- [ ] 2 x 10cm 22AWG cable to connect the Klicky Probe to the Mircofit Terminal
- [ ] Multimeter to check for Continuity 
- [ ] Super Glue

The probe mount wires are also connected with pressure from the magnets, you can use the probe magnets as a template to insert the probe mount magnets, it is easier that way, so that the magnets are not inserted the wrong way.

|  |  |  |  |  |
| :---: | :---: | :---: | :---: | :---: |

You will not lose Y travel on any configuration in the tests that were done.

After everything is assembled let's check again for continuity.



### Step 3.1: Press-fit the magnets

You can now press fit the magnets in place:

<p float="left">
  
  
</p>

Insert the AB mount and probe in the helper parts and you can then press fit with a vice or on a hard surface.

<p float="left">
  
  
  
</p>

### Step 4: AB/SB Mount installation and wiring

For the installation you need the following parts:

- [ ] 2x M3x8 mm SHC Screws



Connect the two wires from the Klicky Probe to the GND and Signal of the recommended Probe signal for your board, you can even leave the BAT85 that is necessary for the 24v inductive probes.
Just take care to leave the +24V of the inductive probe disconnected.

When testing the docking and attachment of the probe, make sure that the back magnet of the probe and the dock magnet do not touch, if they do, it will make attaching the probe much harder.

### Step 5: klipper configuration

Unfortunately, I do not know how to document RRF probe configuration, so here is only Klipper configurations.

As of right now, klipper and RRF have no inbuilt support for a removable probe, fortunately, it does support very robust macro programming, so you will need to add macros to be able to dock and attach the probe as necessary, as well as supporting the rest of the functions that require the usage of a probe.

The macros and instructions on how to configure are located on the [Macro directory](../../../Klipper_macros), you need to **check that before continuing on the build**, there are also some [RRF scripts](../../RRF_macros).

For the printers that are covered here, these are the recommended configuration on the klicky-variables.cfg:

```python
variable_verbose:               True  # Enable verbose output
variable_travel_speed:          200   # how fast all other travel moves will be performed when running these macros
variable_dock_speed:            50    # how fast should the toolhead move when docking the probe for the final movement
variable_release_speed:         75    # how fast should the toolhead move to release the hold of the magnets after docking
variable_z_drop_speed:          20    # how fast the z will lower when moving to the z location to clear the probe
    
variable_safe_z:         	    25    # Minimum Z for attach/dock and homing functions
# if true it will move the bed away from the nozzle when Z is not homed
variable_enable_z_hop:          CHECK_COMMENT  # True on the v2.4, False on v1.8, Trident and Legacy
    
#Dock move (the final movement required to reach the dock and avoid the arms with the probe attached)
Variable_dockmove_x:                40    # Final toolhead movement to release
Variable_dockmove_y:                0     # the probe on the dock
Variable_dockmove_z:                0     # (can be negative)

#Attach move (the final movement required release the probe on the dock)
Variable_attachmove_x:              0     # Final toolhead movement to Dock
Variable_attachmove_y:              30    # the probe on the dock
Variable_attachmove_z:              0     # (can be negative)

```

This example uses the default Voron V2 SKR1.4 configuration, with the probe connected to the P0.10 pin, please update it to your specific configuration.

```python
[probe]
pin: ^P0.10
x_offset: 0
y_offset: 19.75
z_offset: 6.42
speed: 5
samples:3 
samples_result: median
sample_retract_dist: 2.0
samples_tolerance: 0.01
samples_tolerance_retries: 3
```

Also, make sure that the horizontal_move_z on the bed mesh and QGL is high enought that the probe will not hit the bed (needs to be at least 8mm)

```python
[bed_mesh]
horizontal_move_z: 10

[quad_gantry_level]
horizontal_move_z: 10
```

I recommend a probing speed between 3mm/s and 10mm/s, you may experiment to see what is the better speed for your machine.
Please confirm that if you are using the probe input, that the pull-up is enable by using the ^ sign, normally the endstop pins have a hardware solution that does not require this configuration.
Depending on your switch you may need to add a `!` to invert that pin (normally open vs. normally closed).
Normally the endstop pins use a hardware solution, so it is not necessary.

There is now an arrow on the probe telling you where should the switch pole be to have the correct offset.

#### Z endstop and Probe configuration (virtual Z endstop)

If you want to use the Klicky Probe as your Z endstop, please read this [excellent documentation](https://github.com/T4KUUY4/Voron-Stuff/tree/main/KlickyProbeZoffset) by Takuya and Clee.

#### Assembled Klicky Probe

Assembled Klicky Probe

### Step 6: klipper  Dock/Undock configuration
#### Y max position adjustment

If you are using a hall sensor as endstop, you need to make sure that on your Y maximum, the gantry is almost hitting the AB motor mounts, you can have a Y position maximum "behind" the Y endstop position, like this:

```python
[stepper_y]
position_endstop: y
position_max: y+2
```

Even in the stock Y endstop with a lever, you normally can add a extra mm of Y travel due to the lever extra trigger distance:

```python
[stepper_y]
position_endstop: y
position_max: y+1
```

#### Adjust Probe Pickup Position

One of the last things we need to do is to adjust the probe pickup position.

Make sure that the x and y axis are homed and the probe is manually attached to mount, it is easier to do with the hotend and fan duct removed.

Now manually (with gcode commands) move the toolhead to the front  of the probe dock, adjust X so that moving along Y does not hit the dock arms, ***note the X-Position***.

```jinja2
example (for a Ymax of 305):
G0 X20 Y270
G0 X20 Y280 (you see that the right side will hit the dock arm)
G0 X20 Y270
G0 X19 Y270
G0 X19 Y280 (still hitting the dock on the right side)
G0 X19 Y270
G0 X18 Y270
G0 X17 Y280 (now does not hit)

Your variable_docklocation_x is 17

```

Now manually (with gcode commands) move the toolhead to the  Xvariable_docklocation_x Y(max-40) position.
In the example above, it would be "G0 X17 Y265".

The probe and dock magnet can be 1/2 mm away from each other, that is ok, they will attact when the probe is released from the mount.

Now move the toolhead 40mm to the side and check if the probe is docked securely.
If it does, perfect, variable_docklocation_y is your Ymax, if not, you need to either increase the Ymax or add a dock extender and repeat the process.

Open your `klicky-variables.cfg` and find the `#dock location` section and edit the following two line

```python
variable_docklocation_x:
variable_docklocation_y:
```

Test now with the ATTACH_PROBE and DOCK_PROBE if it docks and is removed correctly, some common points that can give problems are:

* the dock magnet is touching the back probe magnet, they cannot touch, push them further in
* the probe is hitting the dock arms, please move the toolhead more to the side where the probe does not hit, by 1mm at a time, until it works
* the probe is falling after being release, the dock is too far away, you can insert one or several 1mm spacer to move the dock and solve this

If you have your Dock mounted to the bed then you need to adjust the `variable_docklocation_z:` too.

#### Automatic Z Calibration

***This requires manual klipper plug-in configuration and installation, it is recommended to be familiar with klipper before attempting this***

If you want to use the Z endstop switch of the Voron to calculate the Z-Offset, use the [automatic Z calibration](https://github.com/protoloft/klipper_z_calibration).
Besides the macros from this repository, you will need to install the Z autocalibration plugin, the recommended way is via [moonraker](https://github.com/protoloft/klipper_z_calibration#moonraker-updater).

Sometimes after installation it's necessary to run the install script manually, if you installed using the moonraker mothod above, run "/home/pi/klipper_z_calibration/install.sh" on the raspberry pi command prompt.

**[I would advise you to read the detailed explanation of the plugin functionality if you want to start using it](https://github.com/protoloft/klipper_z_calibration#how-to-configure-it)**

#### Probe_accuracy and Probe_calibrate

***WARNING when you are doing PROBE_ACCURACY, make sure that the probe is above the bed, the PROBE_ACCURACY macro does not move the toolhead in X or Y.***

## Firsts tests

Before starting to test klicky, and from past mistakes, please remove your PEI sheet (the probe works on the magnetic sheet) and

If possible, change your printer maximum speed, acceleration and Z current, on klipper with TMC steppers, this is how you do it:

```python
SET_TMC_CURRENT STEPPER=stepper_z CURRENT=0.6 
SET_TMC_CURRENT STEPPER=stepper_z1 CURRENT=0.6 
SET_TMC_CURRENT STEPPER=stepper_z2 CURRENT=0.6 
SET_TMC_CURRENT STEPPER=stepper_z3 CURRENT=0.6 
SET_VELOCITY_LIMIT ACCEL=1000
SET_VELOCITY_LIMIT VELOCITY=100
```

Enjoy your Klicky Probe!

## Dock and undock video

https://user-images.githubusercontent.com/16675722/122302371-eb9c4e00-cef9-11eb-91d3-3aded131bae0.mp4

It is working very well, if you decide to use it, give me feedback, either here, or on discord, my discord user is JosAr#0517.

By standing on the shoulders of giants, lets see if we can see further.

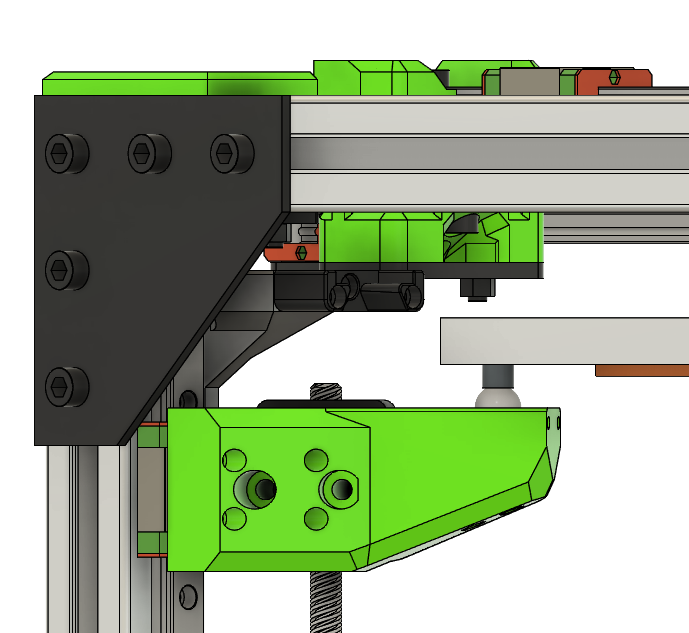
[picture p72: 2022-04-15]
Printers/Ratrig/VCore3/Photos/probe_dock_mount_position.png

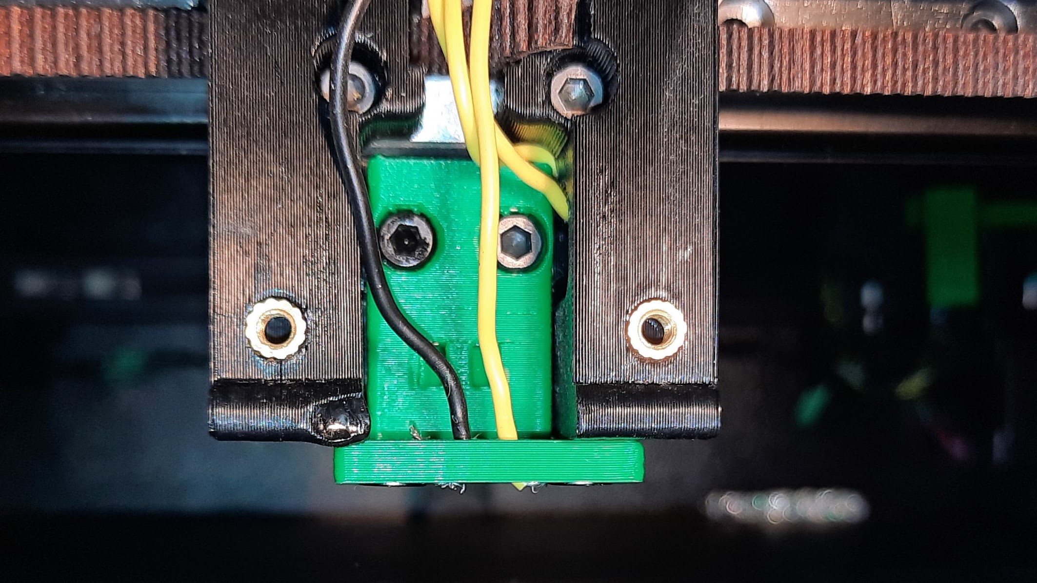
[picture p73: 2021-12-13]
Printers/Voron/Photos/AB_Mount_install_2.jpg

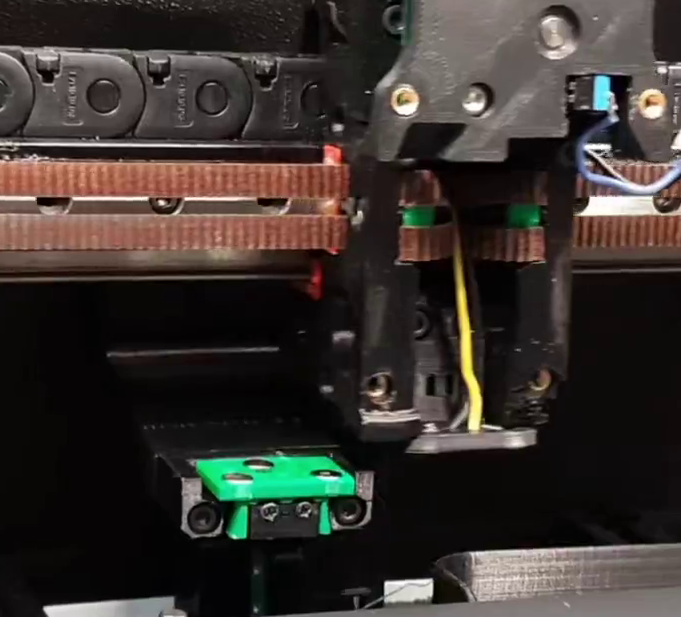
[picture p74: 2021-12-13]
Printers/Voron/Photos/Klicky_Probe installed.png

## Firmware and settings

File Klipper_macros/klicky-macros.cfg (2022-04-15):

# This macro was provided by discord user Garrettwp to whom i give my thanks for sharing it with me.
# I have tweaked it a lot.
# They are based on the great Annex magprobe dockable probe macros "#Originally developed by Mental,
# modified for better use on K-series printers by RyanG and Trails", kudos to them.
# That macro as since evolved into a klipper plugin that currently is pending inclusion in klipper, 
# more information here, https://github.com/Annex-Engineering/Quickdraw_Probe/tree/main/Klipper_Macros
# User richardjm revised the macro variables and added some functions, thanks a lot
# by standing on the shoulders of giants, lets see if we can see further
#
# the current home for this version is https://github.com/jlas1/Klicky-Probe 

[respond]

[gcode_macro _Probe_Variables]
variable_probe_attached:            False
variable_probe_state:               False
variable_probe_lock:                False
variable_z_endstop_x:               0
variable_z_endstop_y:               0
gcode:


#checks if the variable definitions are up to date
[gcode_macro _klicky_check_variables_version]
gcode:
    {% set version = printer["gcode_macro _User_Variables"].version|default(0) %}

    {% if version != 1 %}
        { action_raise_error("Please update your klicky variables, there are some functionality changes") }
    {% endif %}

[gcode_macro _exit_point]
gcode:
    {% set function  = 'pre_' ~ params.FUNCTION %}
    {% set move  = params.MOVE|default(0) %}
    {% set speed = params.SPEED|default(printer["gcode_macro _User_Variables"].travel_speed) %}
    # mandatory to save the new safe position
    M400
    SET_VELOCITY_LIMIT ACCEL={printer.configfile.settings.printer.max_accel}
    SET_VELOCITY_LIMIT ACCEL_TO_DECEL={printer.configfile.settings.printer.max_accel_to_decel}
    RESTORE_GCODE_STATE NAME={function} MOVE={move} MOVE_SPEED={speed}


[gcode_macro _entry_point]
gcode:
    {% set function  = 'pre_' ~ params.FUNCTION %}
    {% set move_accel = printer["gcode_macro _User_Variables"].move_accel|default(1000) %}
    # mandatory to save the new safe position
    M400
    SAVE_GCODE_STATE NAME={function}
    # removes the Z offset for better bed based docking
    SET_GCODE_OFFSET Z=0
    # all the macros initially assume absolute positioning
    G90
    # set a safe(sane) Acceleration
    SET_VELOCITY_LIMIT ACCEL={move_accel}

[gcode_macro _Homing_Variables]
gcode:
    {% set reset  = params.RESET|default(0) %}
    {% if reset %}
        SET_GCODE_VARIABLE MACRO=_Probe_Variables VARIABLE=probe_lock VALUE={ False }
    {% endif %}

##########################
# Attach probe and lock it
[gcode_macro Attach_Probe_Lock]
description: Attaches Klicky Probe, can only be docked after unlocking
gcode:
    Attach_Probe
    _Probe_Lock

########################
# Dock probe and lock it
[gcode_macro Dock_Probe_Unlock]
description: Docks Klicky Probe even if it was locked
gcode:
    _Probe_Unlock
    Dock_Probe

##############
# Unlock Probe
[gcode_macro _Probe_Unlock]
description: Unlocks Klicky Probe state
gcode:
    SET_GCODE_VARIABLE MACRO=_Probe_Variables VARIABLE=probe_lock VALUE={ False }

############
# Lock Probe
[gcode_macro _Probe_Lock]
description: Locks Klicky Probe state
gcode:
    SET_GCODE_VARIABLE MACRO=_Probe_Variables VARIABLE=probe_lock VALUE={ True }

######################
# Attach Probe Routine
[gcode_macro Attach_Probe]
description: Attaches Klicky Probe
gcode:
    # See if the position should be restored after the attach
    {% set goback  = params.BACK|default(0) %}
    # Get probe attach status
    {% set probe_attached = printer["gcode_macro _Probe_Variables"].probe_attached %}
    {% set probe_lock = printer["gcode_macro _Probe_Variables"].probe_lock %}
    {% set verbose = printer["gcode_macro _User_Variables"].verbose %}
    # Get Docking location
    {% set dockmove_x = printer["gcode_macro _User_Variables"].dockmove_x|default(0) %}
    {% set dockmove_y = printer["gcode_macro _User_Variables"].dockmove_y|default(0) %}
    {% set dockmove_z = printer["gcode_macro _User_Variables"].dockmove_z|default(0) %}
    {% set docklocation_x = printer["gcode_macro _User_Variables"].docklocation_x %}
    {% set docklocation_y = printer["gcode_macro _User_Variables"].docklocation_y %}
    {% set docklocation_z = printer["gcode_macro _User_Variables"].docklocation_z %}
    {% set attachmove_x = printer["gcode_macro _User_Variables"].attachmove_x|default(0) %}
    {% set attachmove_y = printer["gcode_macro _User_Variables"].attachmove_y|default(0) %}
    {% set attachmove_z = printer["gcode_macro _User_Variables"].attachmove_z|default(0) %}
    {% set attachmove2_x = printer["gcode_macro _User_Variables"].attachmove2_x|default(0) %}
    {% set attachmove2_y = printer["gcode_macro _User_Variables"].attachmove2_y|default(0) %}
    {% set attachmove2_z = printer["gcode_macro _User_Variables"].attachmove2_z|default(0) %}
    # Safe Z for travel
	{% set safe_z = printer["gcode_macro _User_Variables"].safe_z %}
	{% set enable_z_hop = printer["gcode_macro _User_Variables"].enable_z_hop %}
    # Set feedrates
    {% set travel_feedrate = printer["gcode_macro _User_Variables"].travel_speed * 60 %}
    {% set dock_feedrate = printer["gcode_macro _User_Variables"].dock_speed * 60 %}
    {% set release_feedrate = printer["gcode_macro _User_Variables"].release_speed * 60 %}
    {% set z_drop_feedrate = printer["gcode_macro _User_Variables"].z_drop_speed * 60 %}

    _entry_point function=Attach_Probe

    # If there is no undock movement, fail
    {% if dockmove_x == dockmove_y == dockmove_z == 0 %}
        { action_raise_error("No dockmove location!! To restore old behavior place 40 in dockmove_x") }
    {% endif %}
    # If there is no Attach movement, fail
    {% if attachmove_x == attachmove_y == attachmove_z == 0 %}
        { action_raise_error("No attachmove location!!  To restore old behavior place dockarmslenght value in dockmove_x") }
    {% endif %}

    # If x and y are not homed
    {% if not 'xy' in printer.toolhead.homed_axes %}
        { action_raise_error("Must Home X and Y Axis First!") }

    # If probe not attached and locked
    {% elif not probe_attached and not probe_lock %}
        {% if verbose %}
            { action_respond_info("Attaching Probe") }
        {% endif %}

        {% if not 'z' in printer.toolhead.homed_axes %}
            {% if verbose %}
                { action_respond_info("Resetting Z position to zero") }
            {% endif %}
            SET_KINEMATIC_POSITION Z=0
            {% if not enable_z_hop %} # Disables safe_z
                {% set safe_z = 0 %}
            {% endif %}
        {% endif %}

        # Prior to saving actual position, check if its necessary to move to a safe Z
        # that has enought overhead for the attached probe
        {% if printer.toolhead.position.z < safe_z %}
            {% if verbose %}
                { action_respond_info("moving to a safe Z distance") }
            {% endif %}
            G0 Z{safe_z} F{z_drop_feedrate}
        {% endif %}

        {% if not 'z' in printer.toolhead.homed_axes %}
            {% if verbose %}
                { action_respond_info("Resetting Z position to zero") }
            {% endif %}
            SET_KINEMATIC_POSITION Z=0
        {% endif %}

        {% if printer.toolhead.position.z < safe_z %}
            G0 Z{safe_z} F{z_drop_feedrate}
        {% endif %}

        _Umbilical_Path

        _entry_point function=Attach_Probe_intern

        # if necessary do some actions before moving the toolhead to the docking position
        {% if printer["gcode_macro _DeployDock"] is defined %}
            _DeployDock
        {% endif %}

        # Probe entry location
        G0 X{docklocation_x|int - attachmove_x|int - attachmove2_x|int} Y{docklocation_y|int - attachmove_y|int - attachmove2_y} F{travel_feedrate}
        {% if docklocation_z != -128 %}
            G0 Z{docklocation_z|int - attachmove_z|int - attachmove2_z|int} F{dock_feedrate}
			G0 Z{docklocation_z|int - attachmove_z|int} F{dock_feedrate}
        {% endif %}

        # Drop Probe to Probe location
        {% if docklocation_z != -128 %}
            G0 Z{docklocation_z} F{dock_feedrate}
        {% endif %}
		G0 X{docklocation_x|int - attachmove2_x|int} Y{docklocation_y|int - attachmove2_y} F{travel_feedrate}
        G0 X{docklocation_x} Y{docklocation_y} F{dock_feedrate}

        # Probe Attach
        {% if docklocation_z != -128 %}
        G0 Z{docklocation_z|int - attachmove_z|int} F{z_drop_feedrate}
        {% endif %}
        G0 X{docklocation_x|int - attachmove_x|int} Y{docklocation_y|int - attachmove_y|int} F{release_feedrate}

        # if necessary do some actions after attaching the probe
        {% if printer["gcode_macro _RetractDock"] is defined %}
            _RetractDock
        {% endif %}
		
        # Go to Z safe distance
        {% if printer.toolhead.position.z < safe_z %}
          G0 Z{safe_z} F{z_drop_feedrate}
        {% endif %}
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

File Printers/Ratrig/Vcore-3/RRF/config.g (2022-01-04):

; General preferences
G90                                     ; send absolute coordinates...
M83                                     ; ...but relative extruder moves
M550 P"V-Core 3"                        ; set printer name
M669 K1                                 ; CoreXY
G29 S1                                  ; Set Units to Millimeters

; Network
M552 P0.0.0.0 S1                        ; enable network and acquire dynamic address via DHCP
M586 P0 S1                              ; enable HTTP
M586 P1 S0                              ; disable FTP
M586 P2 S0                              ; disable Telnet

; Drives
M569 P0.0 S0 D3                         ; physical drive 0.0 goes backwards
M569 P0.1 S0 D3                         ; physical drive 0.1 goes backwards
M569 P0.2 S0 D3                         ; physical drive 0.2 goes backwards
M569 P0.3 S1 D2                         ; physical drive 0.3 goes forwards
M569 P0.4 S1 D2                         ; physical drive 0.4 goes forwards
M569 P0.5 S1 D2                         ; physical drive 0.5 goes forwards
M584 X0.4 Y0.3 Z0.0:0.1:0.2 E0.5        ; set drive mapping
M350 X16 Y16 Z16 E16 I1                 ; configure microstepping with interpolation

M92 X80.00 Y80.00 Z800.00               ; set steps per mm
M906 X1200 Y1200 Z800I30               ; set motor currents (mA) and motor idle factor in per cent
M84 S30                                 ; Set idle timeout

M566 X400.00 Y400.00 Z6.00 E300.00 P1          ; set maximum instantaneous speed changes (mm/min)
M203 X10800.00 Y10800.00 Z1000.00 E3600.00     ; set maximum speeds (mm/min)
M201 X4000.00 Y4000.00 Z100.00 E600.00        ; set accelerations (mm/s^2) E3600

; Axis Limits
M208 X-185.25 Y-149 Z0 S1                               ; set axis minima
M208 X185.25 Y149 Z375 S0                         ; set axis maxima

; Endstops
M574 X1 S1 P"xstop"                           ; configure active high endstops
M574 Y2 S1 P"ystop"                           ; configure active high endstops
M574 Z1 S2                                     ; configure Z-probe endstop for low end on Z

M671 X-228.5:-19.5:228.5 Y-169.5:202:-169.5 S5       ; define positions of Z leadscrews or bed levelling screws
M557 X-125:125 Y-130:120 P5                        ; define 5x5 mesh grid

; Heaters
M308 S0 P"bedtemp" Y"thermistor" T100000 B3950 A"Bed"    ; configure sensor 0 as thermistor on pin temp0
M950 H0 C"bedheat" T0                                     ; create bed heater output on out5 and map it to sensor 0
M307 H0 B0 S1.00                                       ; disable bang-bang mode for the bed heater and set PWM limit
M140 H0                                                ; map heated bed to heater 0
M143 H0 S112                                           ; set temperature limit for heater 0 to 110C

;; Run Bed PID Tune!! Bellow is an example for a 300x300 bed
;; M307 H0 A303.1 C356.7 D1.4 S1.00 V24.0 B0
M307 H0 B0 R0.594 C27.1 D3.95 S1.00

; Fans
M950 F0 C"fan0" Q500                   ; create fan 0 on pin out3 and set its frequency
M106 P0 C"Hotend Fan" S0 H1 T45 L255   ; set fan 0 name and value. Thermostatic control turned on for Hotend
M950 F1 C"fan1" Q500                   ; create fan 1 on pin out4 and set its frequency
M106 P1 C"Layer Fan" S0 H-1 L255       ; set fan 1 name and value. Thermostatic control is turned off

; Tools
M563 P0 D0 H1 F1           ; define tool 0
G10 P0 X0 Y0 Z0            ; set tool 0 axis offsets
G10 P0 R0 S0               ; set initial tool 0 active and standby temperatures to 0C

M950 H1 C"e0heat" T1         ; create nozzle heater output on out2 and map it to sensor 1
M307 H1 B0 S1.00           ; disable bang-bang mode for heater and set PWM limit
M143 H1 S300               ; set the maximum temperature in C for heater

; EVA 2 / BMG / E3D V6

M92 E655          ; set extruder steps per mm, bmg wind 1.8deg
M906 E600         ; set extruder motor current (mA) and idle factor in per cent

M308 S1 P"e0temp" Y"thermistor" T100000 B4725 C7.060000e-8 A"Hotend"  
;; Run Heater PID Tune!! 
;; M307 H1 A751.5 C196.6 D4.7 S1.00 V23.9 B0
M307 H1 B0 R2.156 C173.8:95.3 D5.41 S1.00 V24.1

; Z-Probe
M558 P5 C"zprobe.in" H2 F50 T5000 A3       ; set Z probe type to unmodulated and the dive height + speeds
G31 P200 X-17.155 Y-24.826 Z3.861           ; set Z probe trigger value, offset and trigger height, more Z means closer to the bed
;; BLTouch
;M950 S0 C"zprobe.mod"                 ; Create a servo pin on io2
;M558 P9 C"zprobe.in" H10 F240 T10800 A5    ; set Z probe type to unmodulated and the dive height + speeds
;G31 P25 X31 Y-31.75 Z0.978         ; set Z probe trigger value, offset and trigger height, more Z means closer to the bed


M404 N1.75 D0.4                                 ; Filament width and nozzle diameter
T0

; Pressure Advance
; M572 D0 S0.10

; Global variables
global auto_dock = true

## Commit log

2021-12-13 klicky support expantion
    To allow Klicky to support more printer types other than Vorons
    [AB_mount_magnet_holder.stl, AB_mount_magnet_press.stl, AB_mount_press_Helper.stl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]
2021-12-14 VCore3 probe dock and EVA probe mount added
    [Eva probe bracket v15.f3z, Eva probe bracket v15.step, KlickyProbe_Dock_Mount_VCore3.f3z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]
2021-12-20 initial file structure
    [AB_mount_magnet_holder.stl, AB_mount_magnet_press.stl, AB_mount_press_Helper.stl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]
2021-12-31 Add wip macros for RRF on VCore3
    [bed.g, config.g, homez.g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]
2022-01-04 documentation update
    Still a work in progress, this is still unstable
    [AB_mount_magnet_holder.stl, AB_mount_magnet_press.stl, AB_mount_press_Helper.stl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]
2022-01-07 updated Voron printer files
    [1mm_Spacer.stl, AB_mount_magnet_holder.stl, AB_mount_magnet_press.stl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]
2022-01-08 small macros adjustments
    [klicky-bed-mesh-calibrate.cfg, klicky-macros.cfg, klicky-probe.cfg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]
2022-01-22 bender initial setup
    [klicky-probe.cfg, klicky-variables.cfg, klicky-z-calibration.cfg]
2022-01-22 Bender Defaults
    [klicky-variables.cfg, klicky-z-calibration.cfg]
2022-04-15 update config
    [klicky-quad-gantry-level.cfg, klicky-variables.cfg, klicky-z-calibration.cfg]
